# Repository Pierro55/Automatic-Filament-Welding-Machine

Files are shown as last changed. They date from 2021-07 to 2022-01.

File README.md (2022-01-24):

# REuse: Automatic Filament Welding Machine

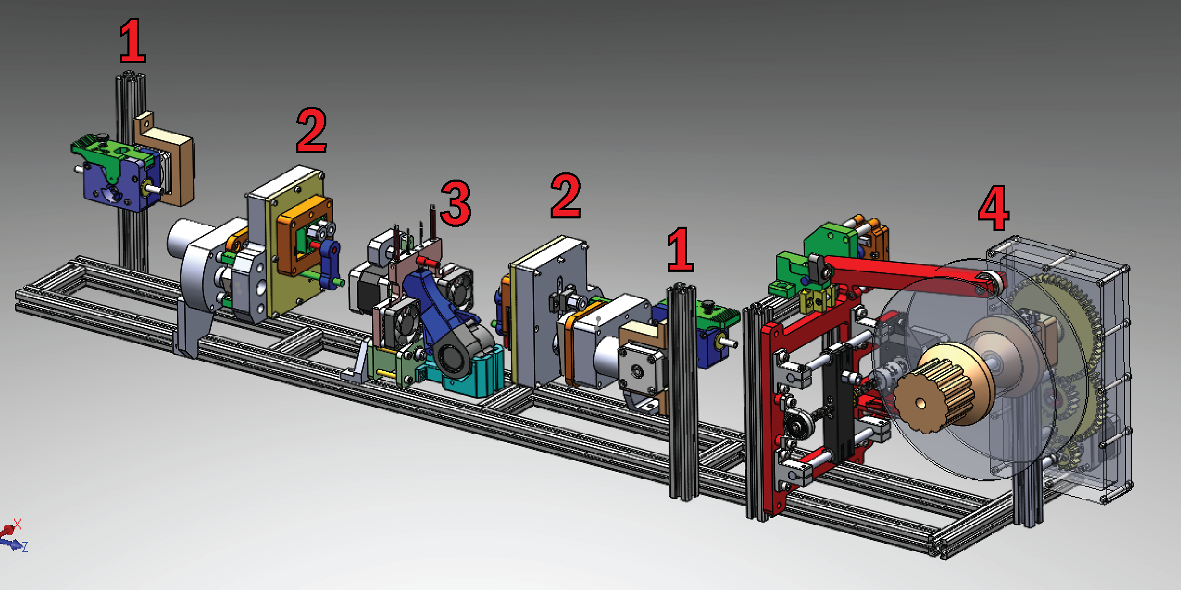
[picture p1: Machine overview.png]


## What is this?
This is an automatic filament welding machine made for 3mm (or 2.85mm) filament. Its purpose is to weld left over filament and wind it on a spool afterwards. The system can be adapted for 1.75mm if needed. 

## General information
I've designed and build this machine as part of my mechanical engineering bachelor thesis. Unfortunately, I didn't had enough time to program and test it thoroughly but tested every single subsystem of the machine itself. The welding part itself works really well. 
All parts are modular and interchangeable. I’ve attached my thesis report which goes into every little detail of the design and building process. It is written in Dutch but translating it should be doable. Maybe I will add an English version in the near future if I get enough requests (or maybe somebody else is so kind to translate it). If you can understand Dutch, please read it with a grain of salt as Dutch isn’t my first language. I will roughly describe every process in English in each folder.
I don't have the machine on hand because I have built it for a company so I cannot make it fully working unfortunately as I don’t have the financial medium to build one myself. Nevertheless, I wanted to make this open source as I have learned a lot through the open source movement about 3D printing and I wanted to give something back to the community. 

If you have any question please do not hesitate to send me a DM on Discord: Pierro55#4076

## Disclaimer
If you try to replicate this machine with the provided data, make sure you work safe. This information is provided for free under the terms of the GPL-2.0 License. Everything is provided without any warranty of any kind. Use the provided information at your own risk, any damage to a machine, device, yourself or similar is solely your own responsibility.

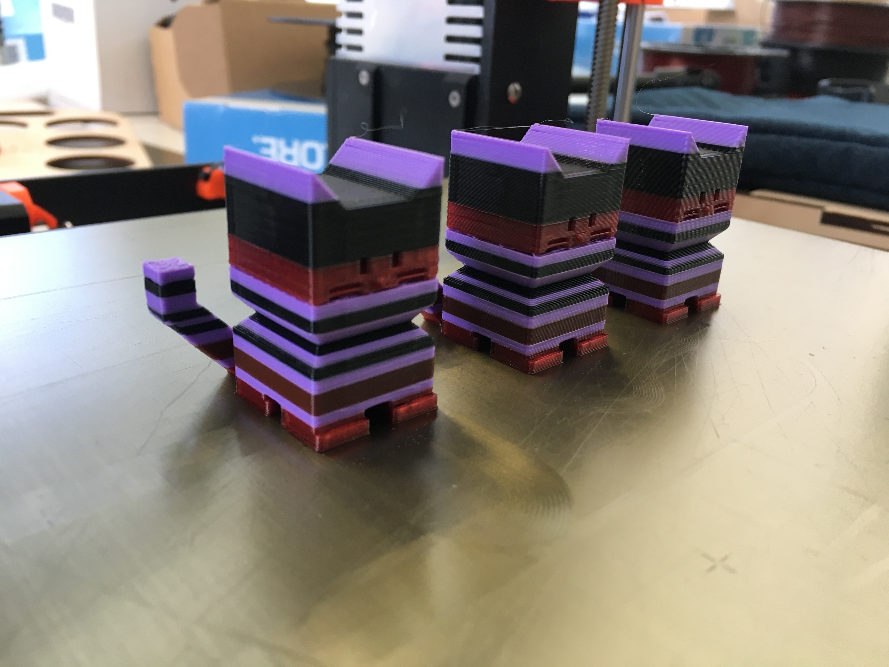
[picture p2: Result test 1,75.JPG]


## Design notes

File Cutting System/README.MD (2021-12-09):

# Cutting system

The cutting system is designed to cut off the filament ends before welding them together and automatically eject the cutoff. The idea behind this system is to make the machine more reliable by controlling the shape of the filament ends. In my experiments I used a geared DC motor for this, which turned out to be too weak. I therefore had to ditch it for the final machine as there wasn’t enough time left. It can still be added to the machine because of its modularity.

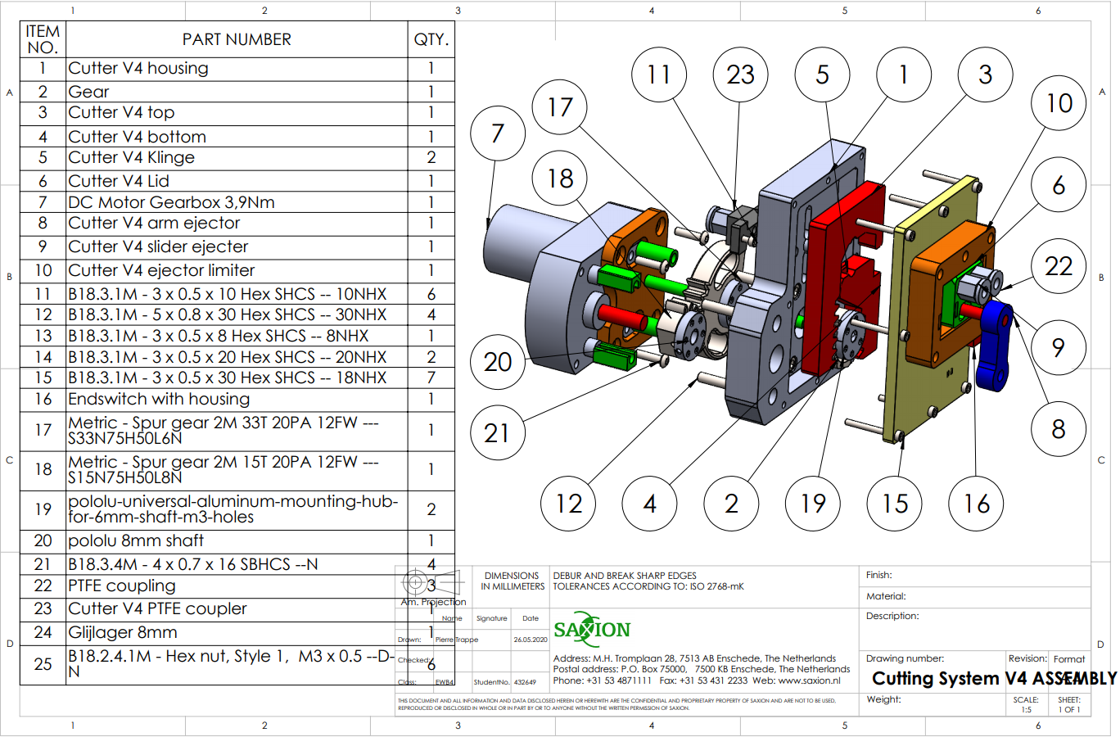
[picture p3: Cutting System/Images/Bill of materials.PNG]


### Basic Principle
The basic principle works as follows:

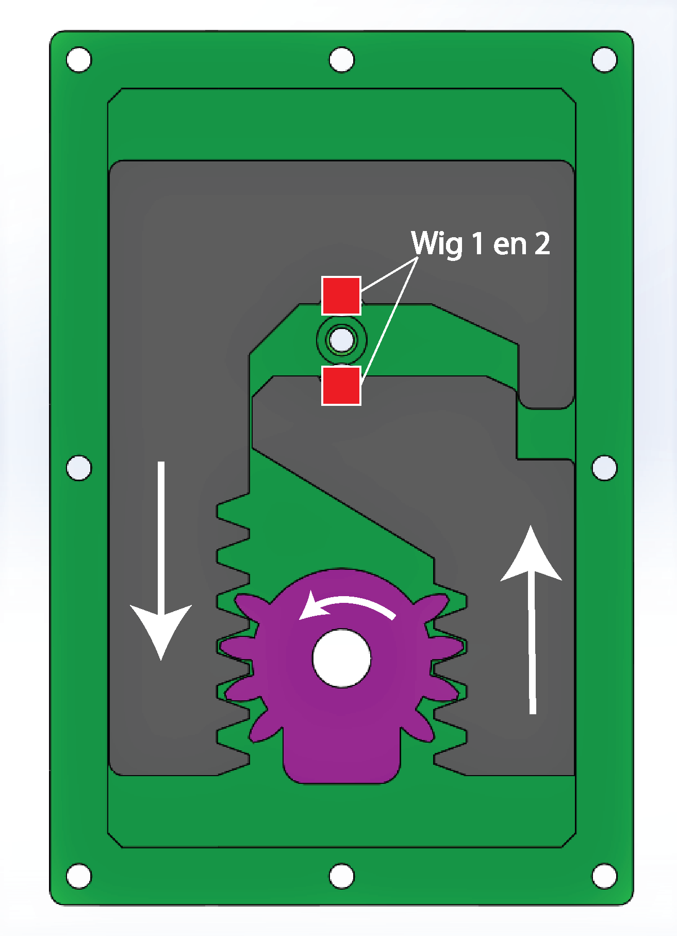
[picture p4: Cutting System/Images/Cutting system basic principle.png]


The purple gear is connected to the motor. This gear moves the left brown arm through a rag pinion mechanism down and the right one up (and vice versa if the motor rotates the other direction). Both arms have a wedge (wig in Dutch) mounted in the middle. As the arms move closer to each other the wedge cuts off filament which sits in the hole between the two arms.
The automatic ejection happens on the outside of the cutting system. As the motor moves the mechanism, a second mechanism, which is directly coupled with the motor shaft, moves two outputs. One is for the cutoff and the second one is for the to be welded filament. 

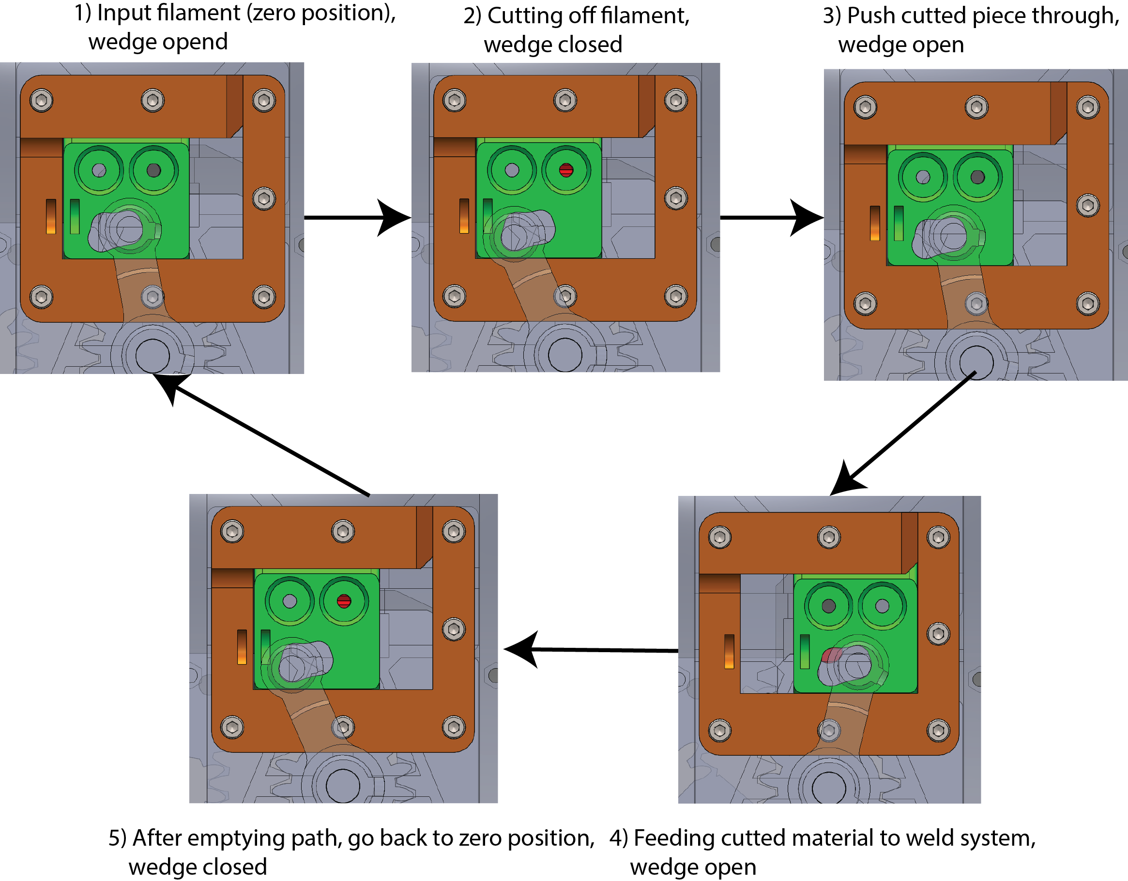
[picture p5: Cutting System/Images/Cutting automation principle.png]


Some rl photos

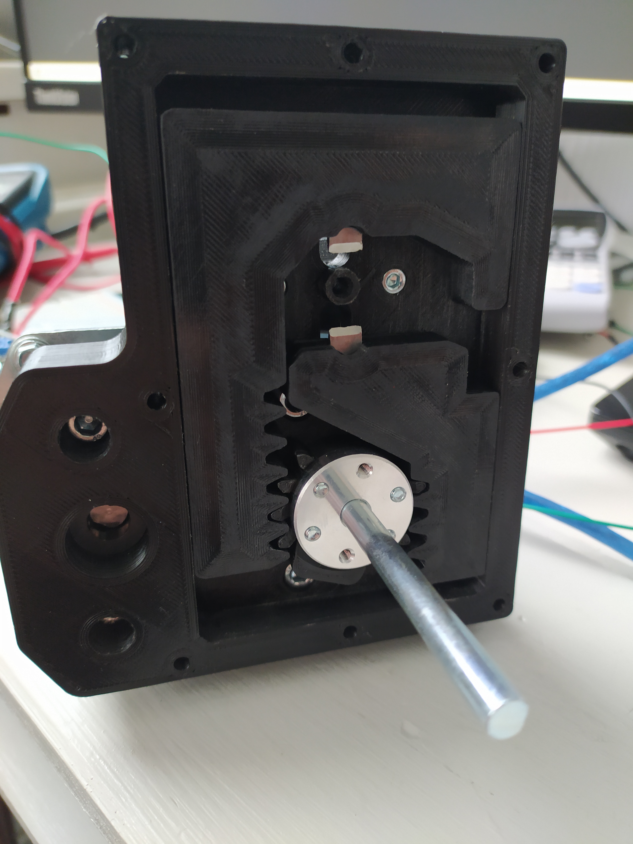
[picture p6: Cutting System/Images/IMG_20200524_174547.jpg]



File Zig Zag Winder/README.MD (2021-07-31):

## Zig Zag Winder

This part of the machine basically takes care of a neat winding of the welded material. It moves the welded material in a zig zag manner when winding it onto a spool.

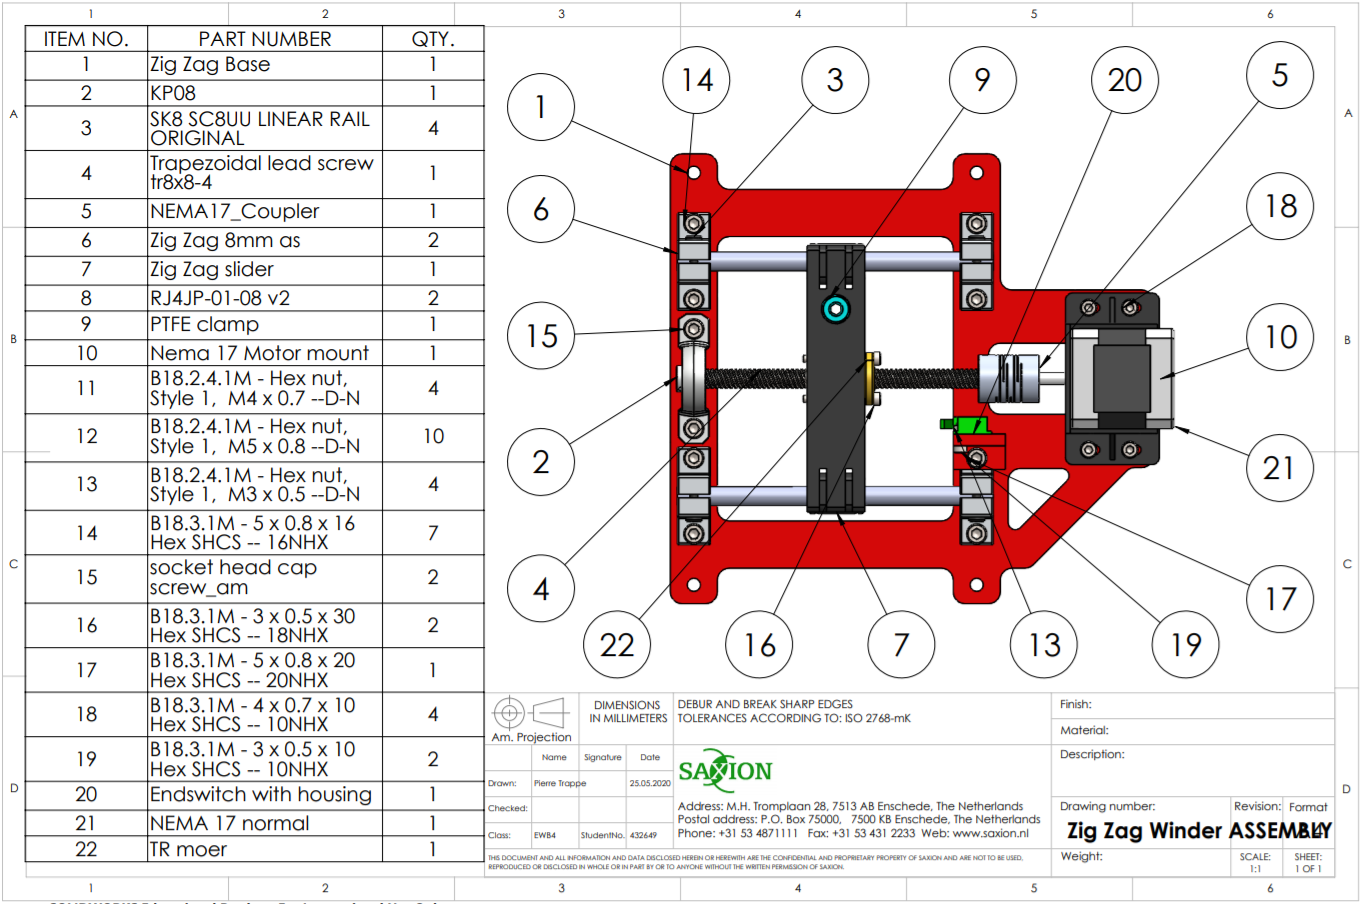
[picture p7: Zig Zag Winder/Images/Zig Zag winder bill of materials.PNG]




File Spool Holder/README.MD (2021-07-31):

# Spool Holder

This part of the machine is designed to drive the winding action and to accept various types of filaments spools. It self-centers the spool when mounting it on the device. It uses a small Nema 17 motor with some gears to beef it up as no fast speeds are needed. It can fit bigger spools when using a longer shaft.

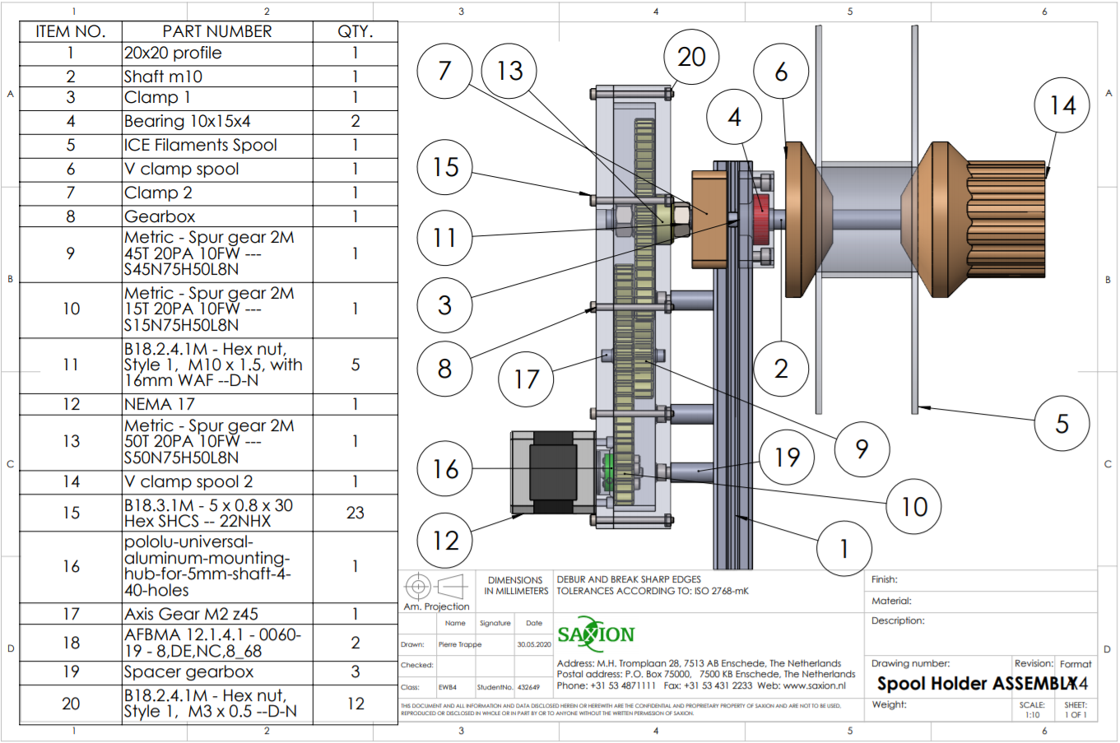
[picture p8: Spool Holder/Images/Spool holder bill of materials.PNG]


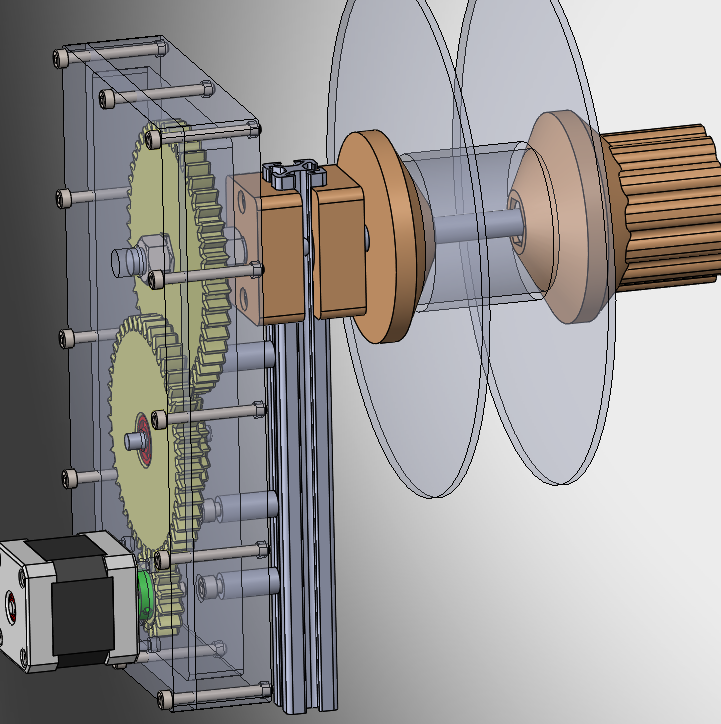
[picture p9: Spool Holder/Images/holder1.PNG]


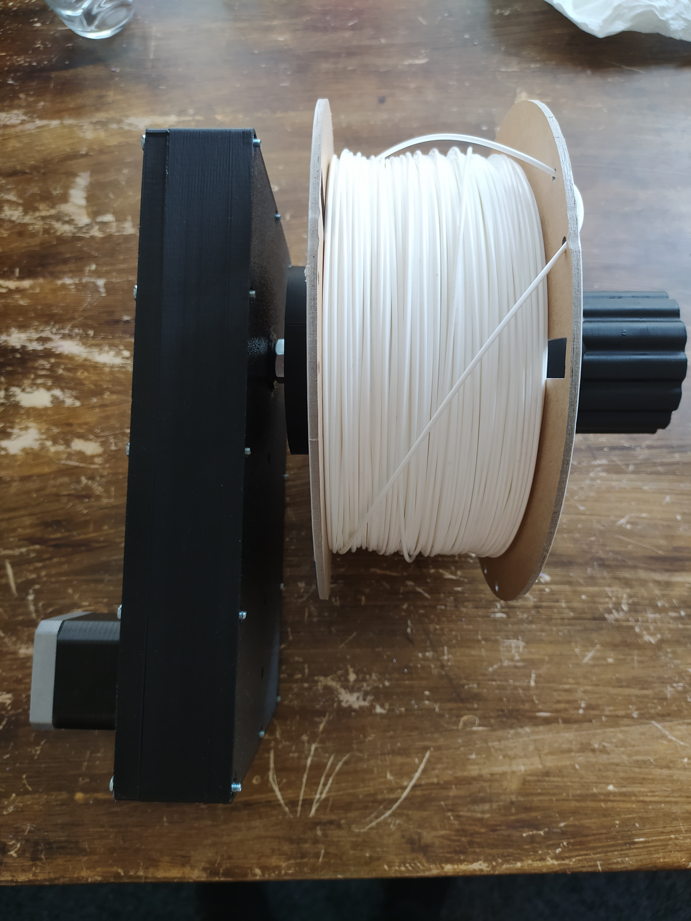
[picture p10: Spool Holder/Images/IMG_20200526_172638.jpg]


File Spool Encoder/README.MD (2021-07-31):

# Spool encoder
This part of the machine keeps track of the material on the spool. This is needed to get information on when the spool is full and also for setting the right winding speed. 

It is basically an arm which sits directly on the spool. The axis of this arm is connected to a potentiometer. As material builds up, the arm goes up and therefore the value of the potentiometer changes. This value gets converted in the software and can be used for said purposes. 

It can be mounted to a 20x20 aluminum extrusion profile.
For ease of use when unmounting a spool, a latch is included in the design to hold the arm up while changing spools.

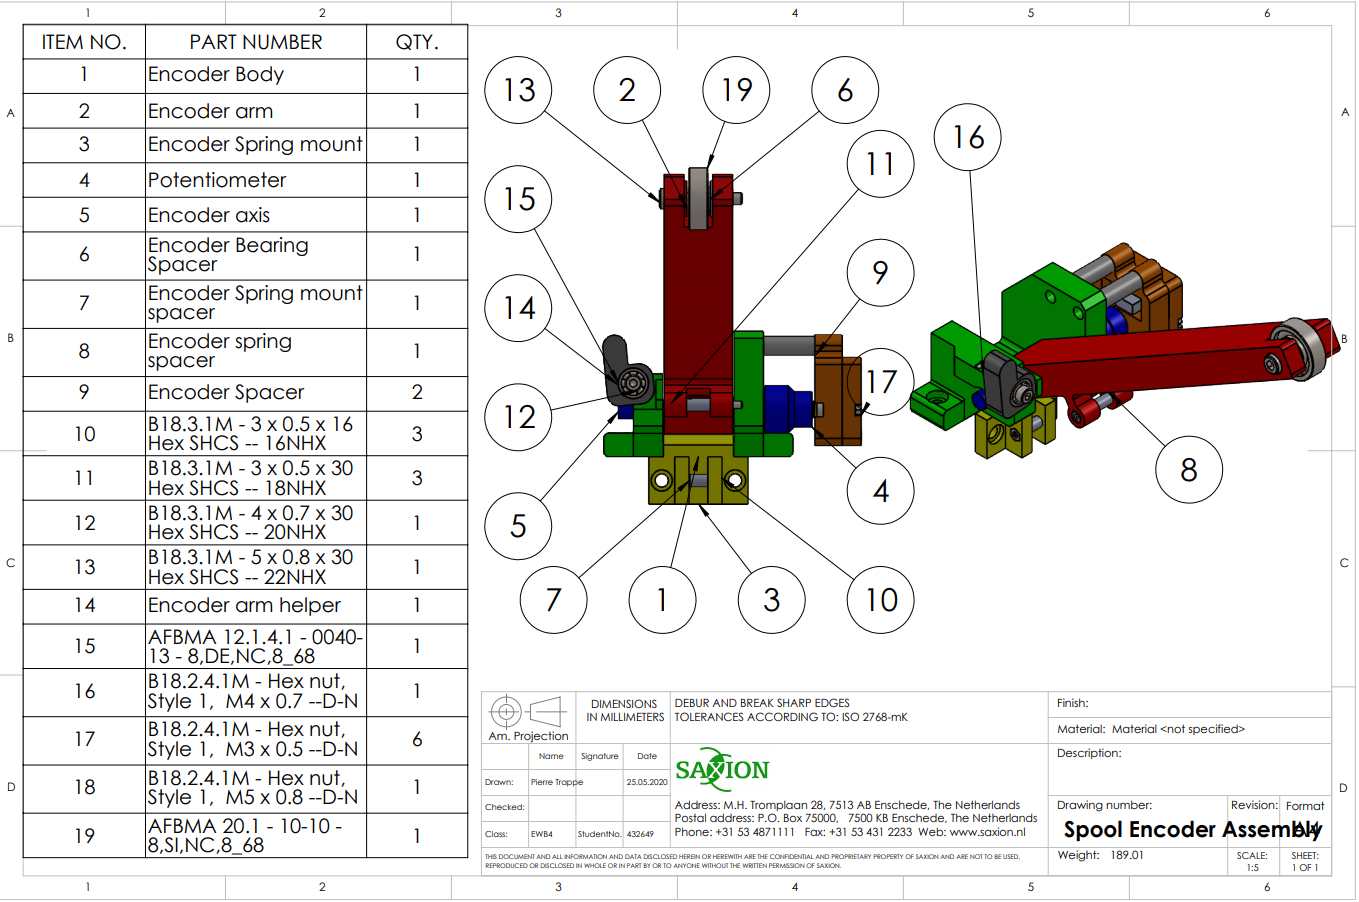
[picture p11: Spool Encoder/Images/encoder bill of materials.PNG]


,

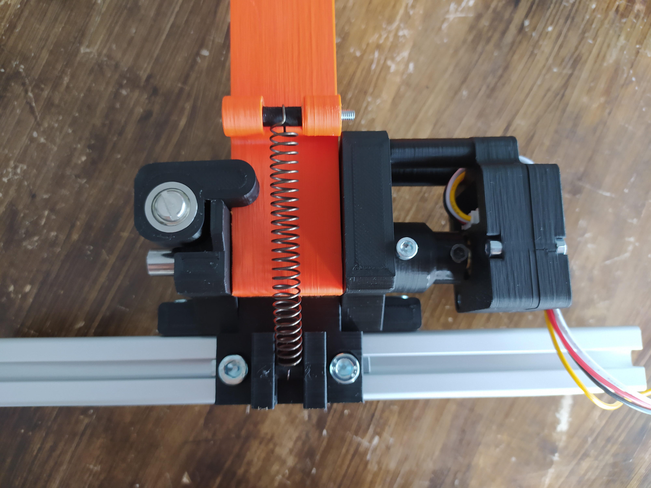
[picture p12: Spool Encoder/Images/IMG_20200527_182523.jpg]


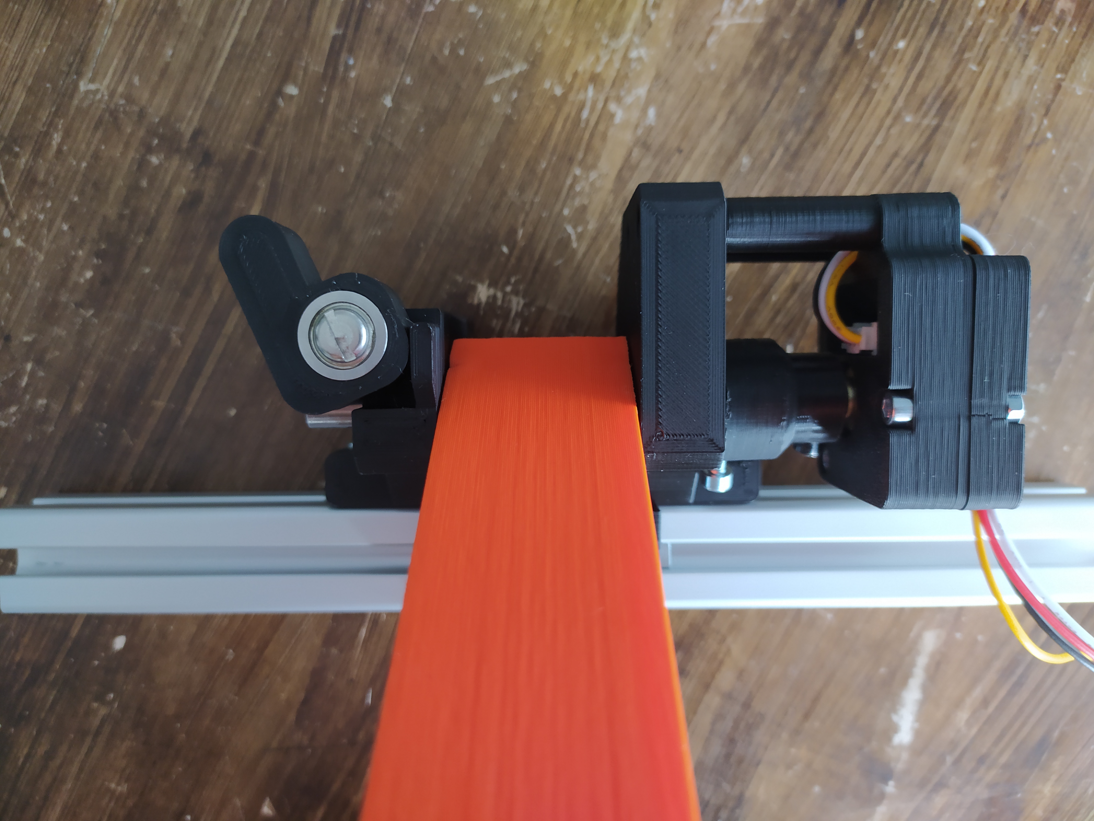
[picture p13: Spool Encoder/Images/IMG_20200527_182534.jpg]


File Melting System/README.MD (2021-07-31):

# Melting System

The melting system can weld two pieces of filament together and also cool the weld afterwards. A first movement test can be seen in the following video:

https://user-images.githubusercontent.com/57869093/126063074-c9a9bbb9-c436-44e4-bffa-66c6a044f957.mp4

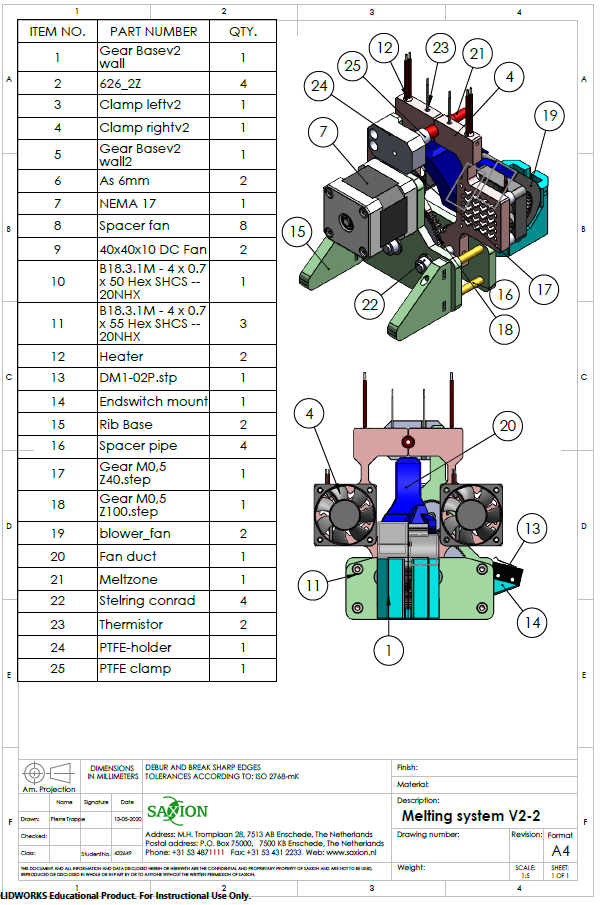
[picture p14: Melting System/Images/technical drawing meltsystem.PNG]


The melt zone itself is made out of PTFE with a honed inner surface of 2.9mm in diameter. The system functions basically as a hotend seen on FDM 3D printers. It has a hot zone and an active cooled cold zone. Two clamps are moved simultaneously to either enabling welding or cooling. 
A result of the welding process can be seen in the following picture:

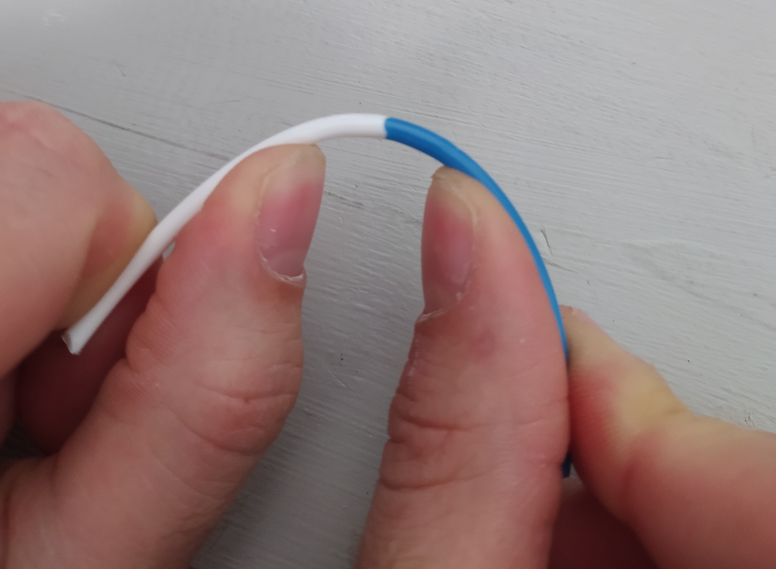
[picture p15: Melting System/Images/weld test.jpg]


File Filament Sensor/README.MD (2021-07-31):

# Filament Sensor

The filament sensor has the purposes to locate the filament position on various locations in the machine. 

The sensor housing uses a compliant mechanism to trigger the mechanical endstop when filament is detected. 

A grooved bearing makes the system bidirectional to ensure that filament can travel back and forth without getting pinched resulting in a jam.

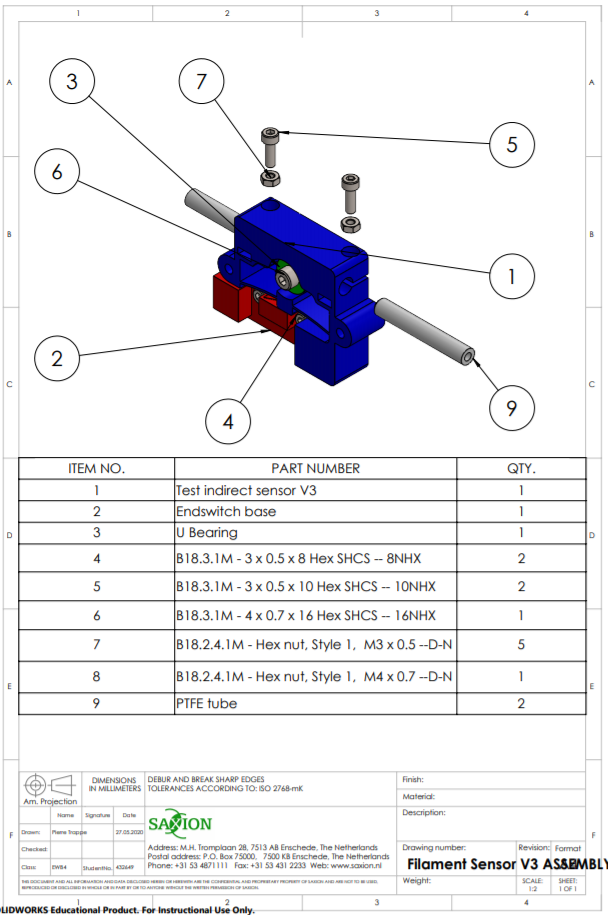
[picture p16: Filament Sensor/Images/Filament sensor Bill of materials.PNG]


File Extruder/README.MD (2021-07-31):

## Extruder

The extruder has the purpose of moving filament through the system. In the final machine, two extruders are used as both ends of filaments needs to be moved individually.

This extruder design uses original Bondtech hardware (hobbed gears, shafts, bearings, 5:1 geared motor...). The housing is 3D printed. 
This design uses 3mm filament. 

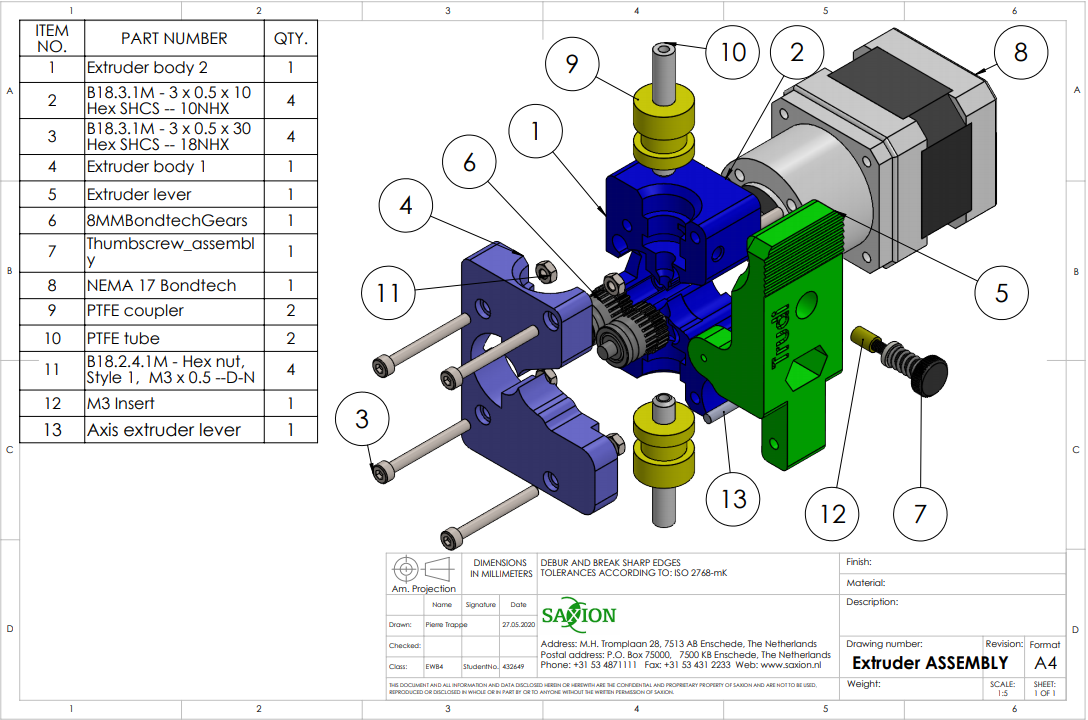
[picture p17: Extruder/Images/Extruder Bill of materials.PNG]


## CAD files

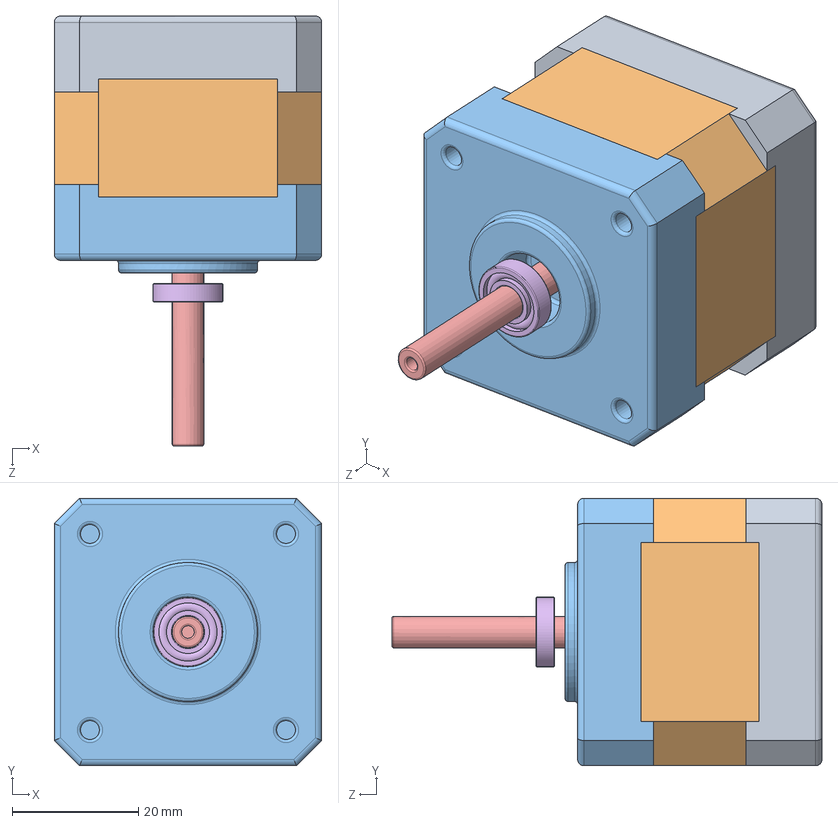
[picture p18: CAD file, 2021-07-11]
Extruder/CAD/NEMA 17.SLDASM
42.3 x 42.3 x 68.0 mm
Base
Cuerpo
Tapa
pan cross head_am x 4
Eje
instrument ball bearing_68_am x 2

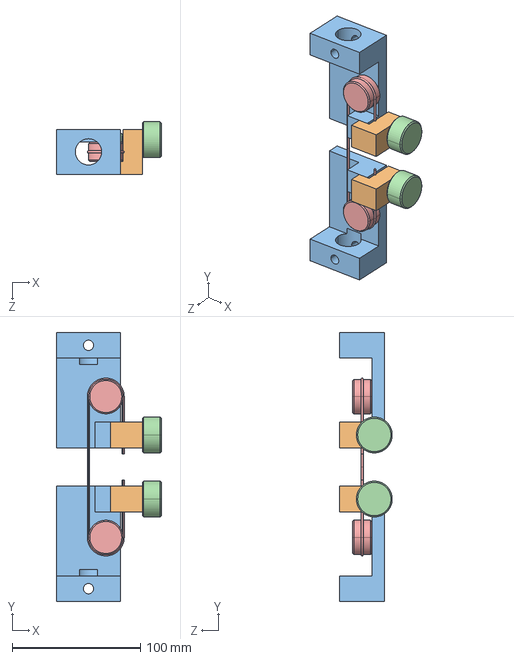
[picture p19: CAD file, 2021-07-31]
Tensile Strength Tester/CAD/Filamenttester ASSEMBLY.STEP
82.0 x 210.0 x 41.0 mm
Filament tester
Filament tester mirrored

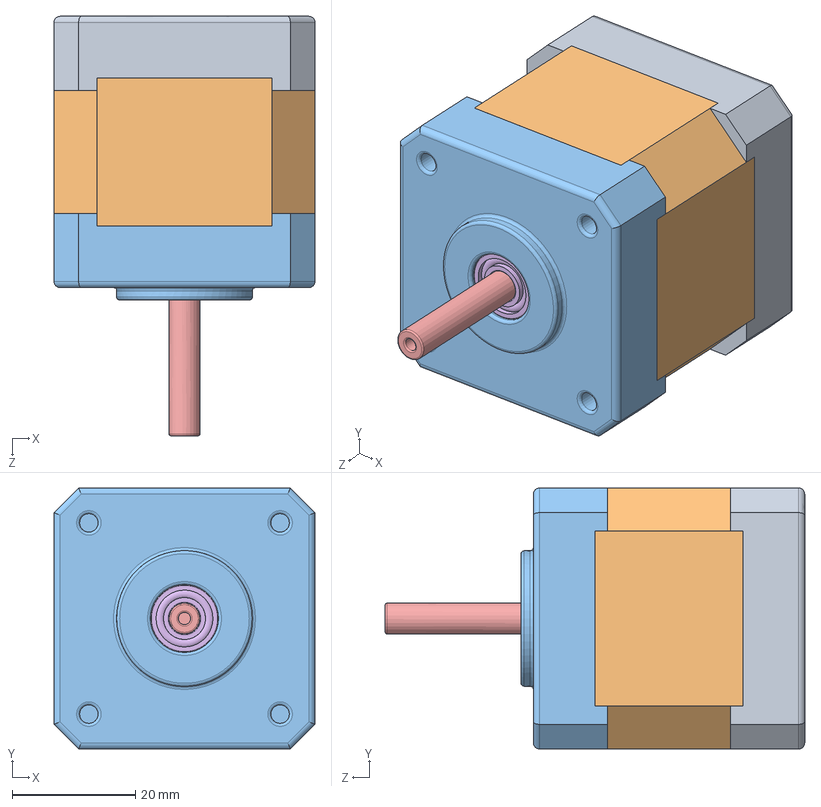
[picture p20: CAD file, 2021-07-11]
Cutting System/CAD/NEMA 17.SLDASM
42.3 x 42.3 x 68.0 mm
Base
Cuerpo
Tapa
pan cross head_am x 4
Eje
instrument ball bearing_68_am x 2

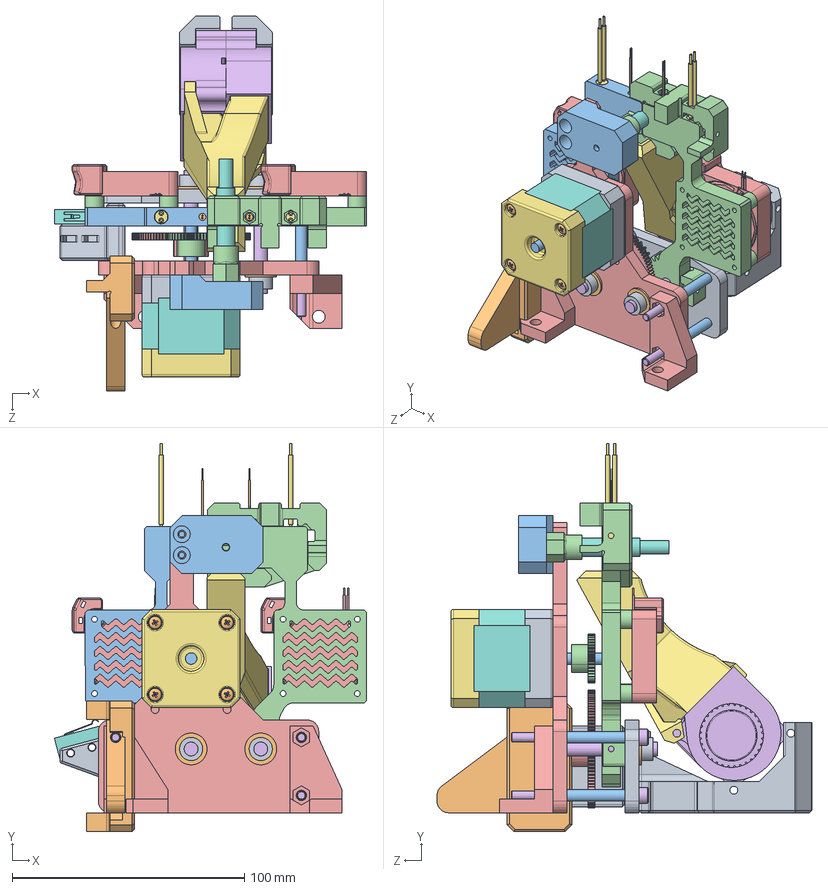
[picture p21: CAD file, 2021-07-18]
Melting System/CAD/Melting system V2-2.SLDASM
134.5 x 167.3 x 161.5 mm
Gear Basev2 wall
626_2Z x 4
Clamp leftv2
Clamp rightv2
Gear Basev2 wall2
As 6mm x 2
Base
Cuerpo
Tapa
pan cross head_am x 4
Eje
Spacer fan x 8
40x40x10 DC Fan x 2
socket head cap screw_am x 4
Heater x 2
DM1-02P.stp
Endswitch mount
Spacer pipe x 4
Gear M0,5 Z40.step
Gear M0,5 Z100.step
blower_fan x 2
Fan duct
Meltzone
Stelring conrad x 4
Thermistor x 2
PTFE-holder
PTFE clamp

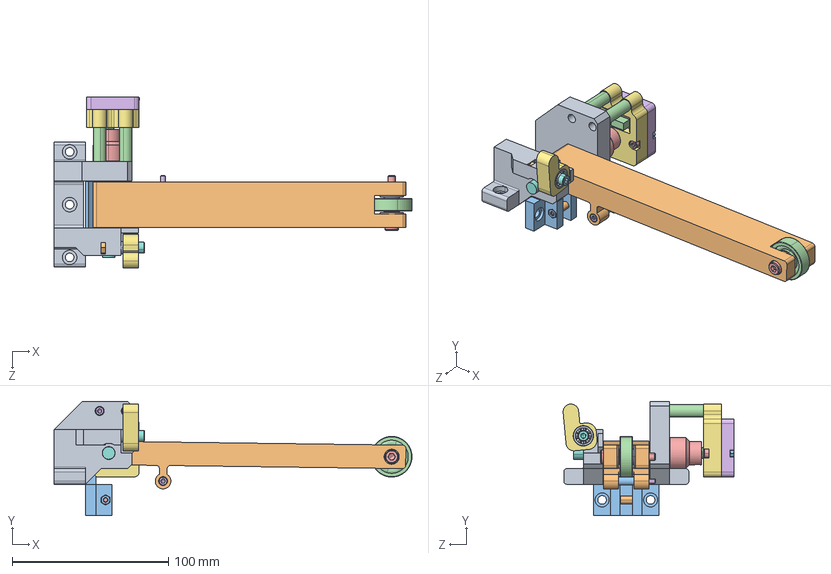
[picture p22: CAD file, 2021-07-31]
Spool Encoder/CAD/Spool Encoder ASSEMBLY.STEP
229.0 x 73.0 x 109.3 mm
Encoder Body
Encoder arm
Encoder Spring mount
Potentiometer
Encoder axis
Encoder Bearing Spacer
Encoder Spring mount spacer
Encoder spring spacer
Encoder Spacer x 2
socket head cap screw_am_B18.3.1M - 3 x 0.5 x 16 Hex SHCS -- 16NHX x 3
socket head cap screw_am_B18.3.1M - 3 x 0.5 x 30 Hex SHCS -- 18NHX x 3
Encoder arm helper
socket head cap screw_am_B18.3.1M - 4 x 0.7 x 30 Hex SHCS -- 20NHX
instrument ball bearing_68_am_AFBMA 12.1.4.1 - 0040-13 - 8,DE,NC,8_68
hex nut style 1_am_B18.2.4.1M - Hex nut, Style 1, M4 x 0.7 --D-N
hex nut style 1_am_B18.2.4.1M - Hex nut, Style 1, M3 x 0.5 --D-N x 6
radial ball bearing_68_am_AFBMA 20.1 - 10-10 - 8,SI,NC,8_68
socket head cap screw_am_B18.3.1M - 5 x 0.8 x 30 Hex SHCS -- 22NHX
hex nut style 1_am_B18.2.4.1M - Hex nut, Style 1, M5 x 0.8 --D-N

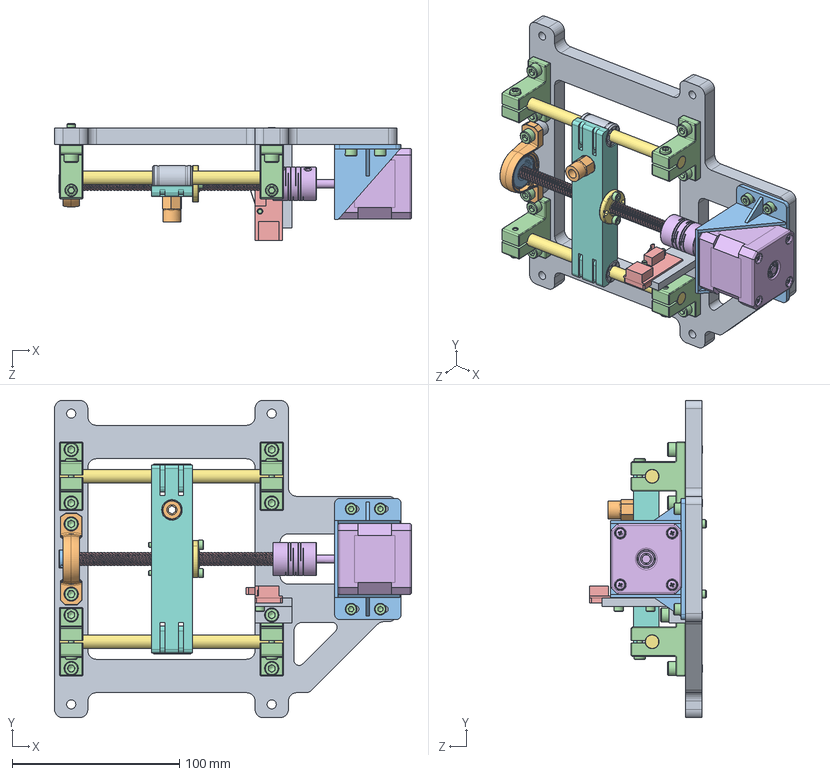
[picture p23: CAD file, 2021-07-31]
Zig Zag Winder/CAD/Zig Zag Winder ASSEMBLY.SLDASM
213.6 x 190.0 x 69.9 mm
Zig Zag Base
KP08
608RS
SK8 SC8UU LINEAR RAIL ORIGINAL x 4
Trapezoidal lead screw tr8x8-4
NEMA17_Coupler
Zig Zag 8mm as x 2
Zig Zag slider
RJ4JP-01-08 v2 x 2
PTFE clamp
Nema 17 Motor mount
socket head cap screw_am x 18
Endswitch with housing
NEMA 17 normal
TR moer

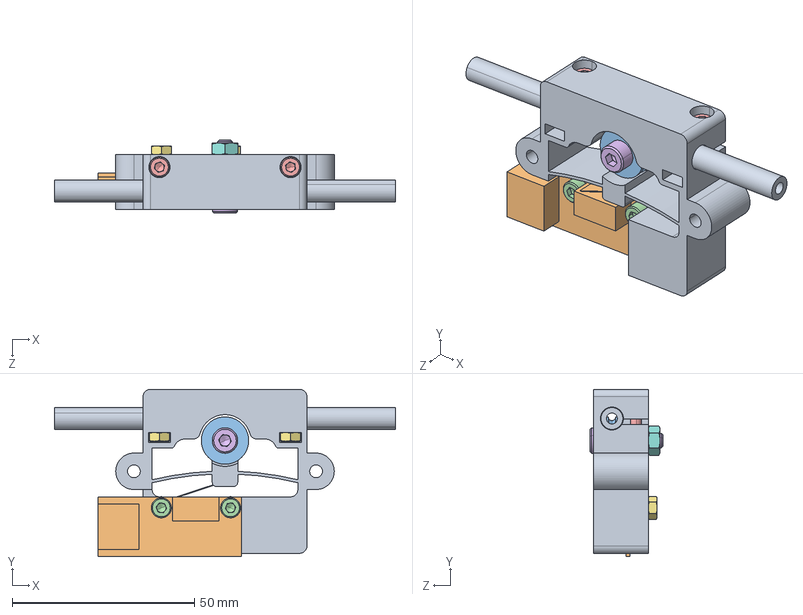
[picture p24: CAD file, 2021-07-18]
Filament Sensor/CAD/Filament Sensor V3 ASSEMBLY.STEP
93.6 x 45.9 x 20.0 mm
Test indirect sensor V3
Endswitch base
U Bearing
socket head cap screw_am_B18.3.1M - 3 x 0.5 x 8 Hex SHCS -- 8NHX x 2
socket head cap screw_am_B18.3.1M - 3 x 0.5 x 10 Hex SHCS -- 10NHX x 2
socket head cap screw_am_B18.3.1M - 4 x 0.7 x 16 Hex SHCS -- 16NHX
hex nut style 1_am_B18.2.4.1M - Hex nut, Style 1, M3 x 0.5 --D-N x 5
hex nut style 1_am_B18.2.4.1M - Hex nut, Style 1, M4 x 0.7 --D-N
PTFE tube x 2

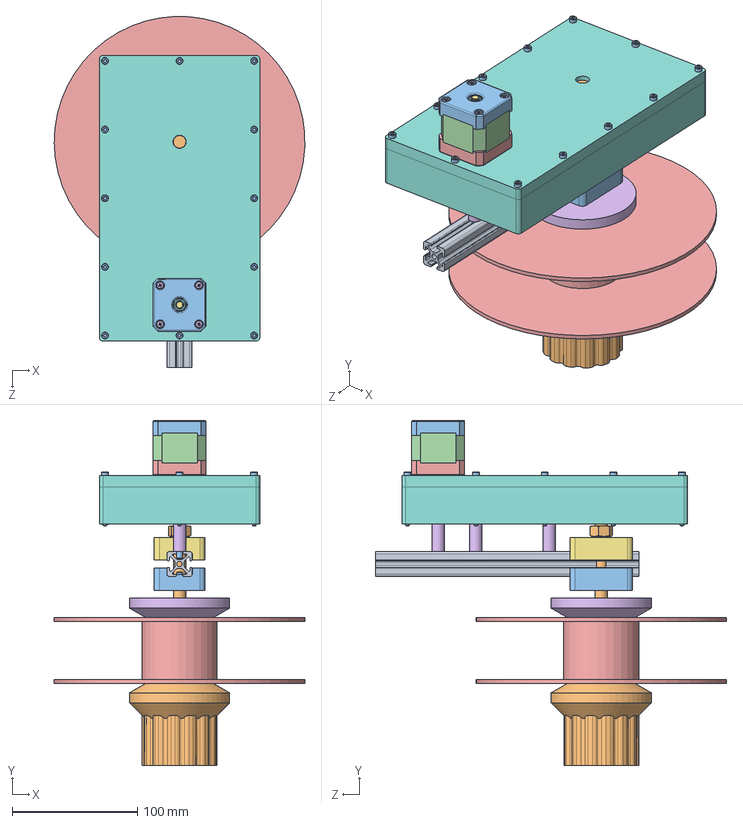
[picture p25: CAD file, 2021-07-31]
Spool Holder/CAD/Spool Holder ASSEMBLY.SLDASM
199.9 x 275.2 x 279.9 mm
20x20 profile
Shaft m10
Clamp 1
Bearing 10x15x4 x 2
ICE Filaments Spool
V clamp spool
Clamp 2
Gearbox
spur gear_am x 3
hex nut style 1_am x 17
Base
Cuerpo
Tapa
pan cross head_am x 4
Eje
instrument ball bearing_68_am x 4
Gear m2 z20
V clamp spool 2
socket head cap screw_am x 23
pololu-universal-aluminum-mounting-hub-for-5mm-shaft-4-40-holes
Axis Gear M2 z45
Spacer gearbox x 3

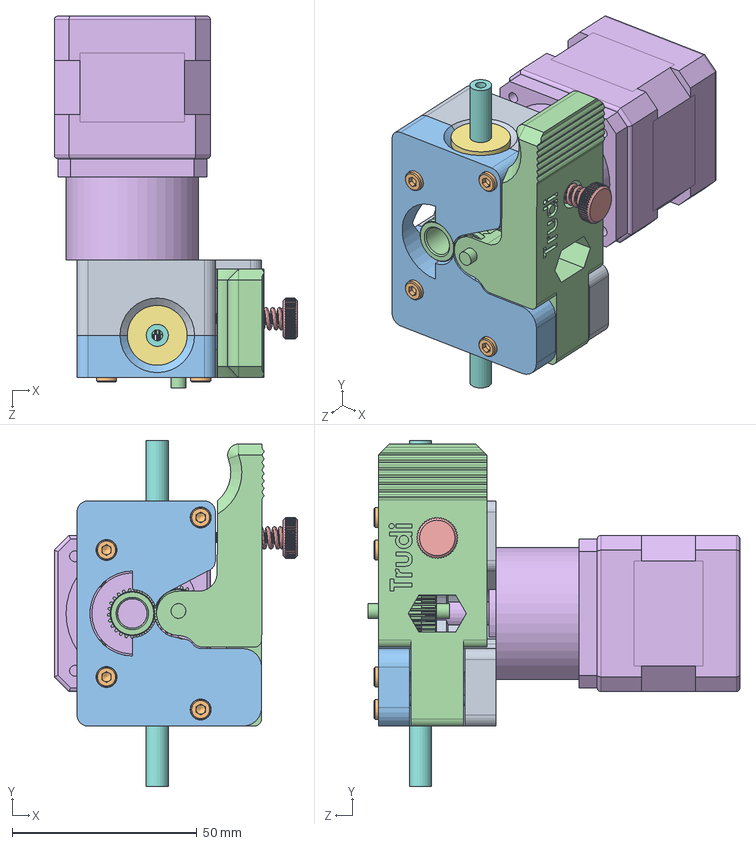
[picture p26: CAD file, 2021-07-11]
Extruder/CAD/Extruder ASSEMBLY.SLDASM
65.9 x 93.7 x 100.7 mm
Extruder body 2
socket head cap screw_am x 8
Extruder body 1
Extruder lever
Thumbscrew_assembly
NEMA 17 Bondtech
PTFE coupler x 2
PTFE tube x 2
hex nut style 1_am x 4
M3 Insert
Axis extruder lever
8MMBondtechGears

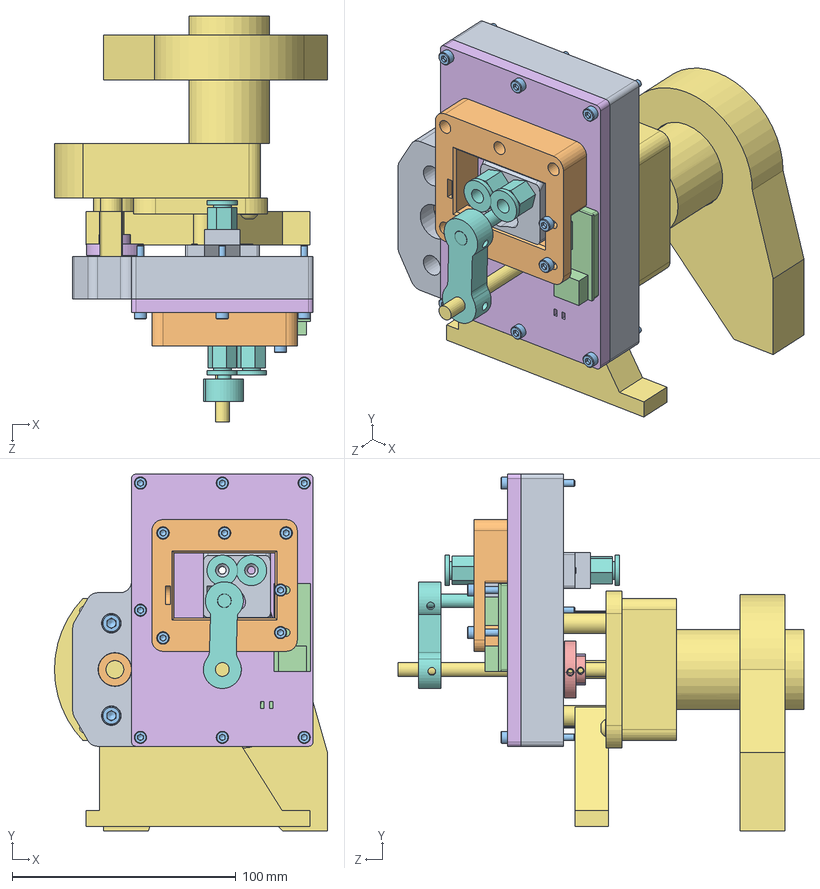
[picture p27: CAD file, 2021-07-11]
Cutting System/CAD/Cutting System V4 ASSEMBLY.SLDASM
122.0 x 159.4 x 181.4 mm
Cutter V4 housing
Gear
Cutter V4 top
Cutter V4 bottom
Cutter V4 Klinge x 2
Cutter V4 Lid
DC Motor Gearbox 3,9Nm
Cutter V4 arm ejector
Cutter V4 slider ejecter
Cutter V4 ejector limiter
socket head cap screw_am x 20
Endswitch with housing
pololu-universal-aluminum-mounting-hub-for-6mm-shaft-m3-holes x 2
pololu 8mm shaft
socket button head cap screw_am x 4
PTFE coupling x 3
Cutter V4 PTFE coupler
Glijlager 8mm
hex nut style 1_am x 6

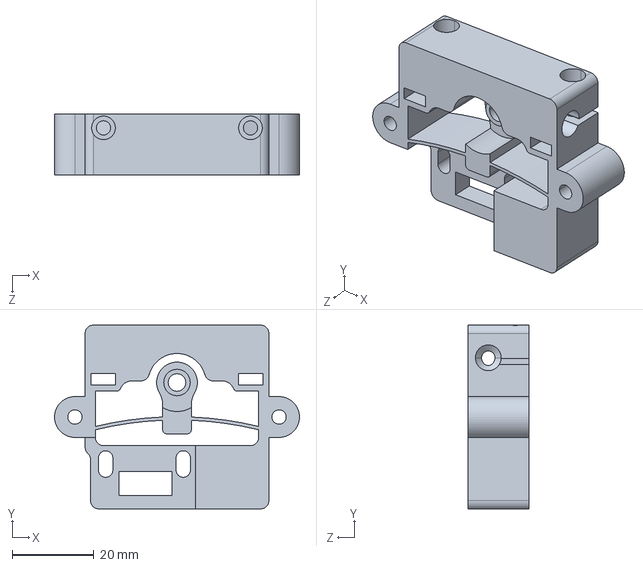
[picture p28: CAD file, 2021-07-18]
Filament Sensor/CAD/Test indirect sensor V3.STEP
60.0 x 45.0 x 15.0 mm

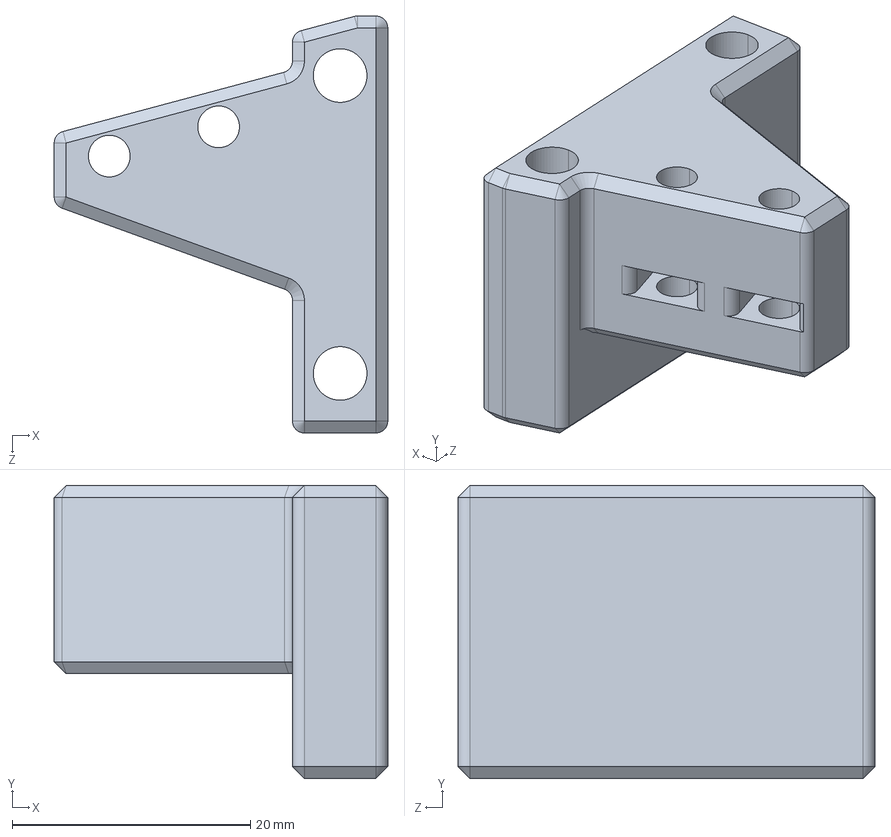
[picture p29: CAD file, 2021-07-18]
Melting System/CAD/Endswitch mount.STEP
28.0 x 24.6 x 35.0 mm

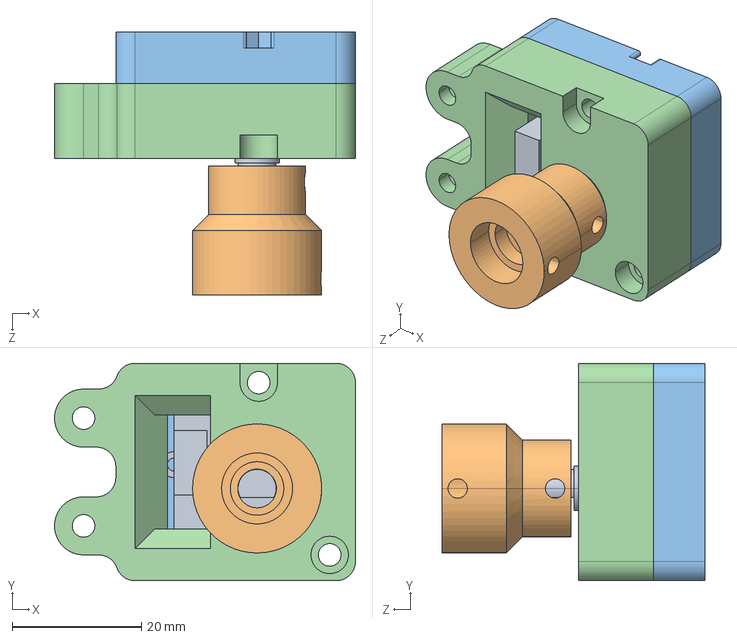
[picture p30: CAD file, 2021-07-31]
Spool Encoder/CAD/Potentiometer.STEP
46.6 x 33.7 x 40.8 mm

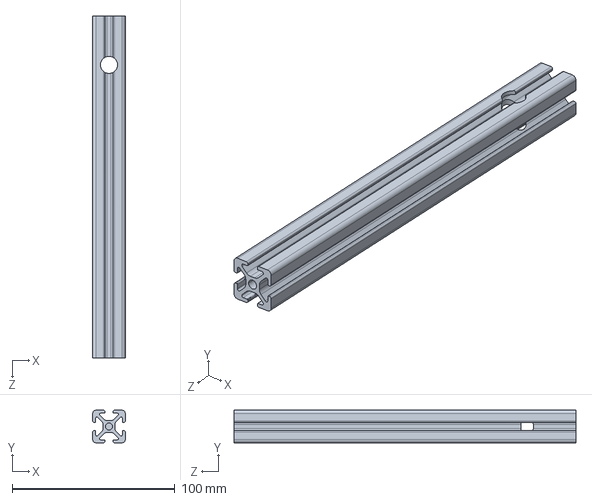
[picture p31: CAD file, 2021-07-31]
Spool Holder/CAD/20x20 profile.STEP
20.0 x 20.0 x 210.0 mm

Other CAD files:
Cutting System/CAD/626_Z.sldasm
Zig Zag Winder/CAD/PTFE clamp.STEP
Extruder/CAD/Extruder body 2.STEP
Filament Sensor/CAD/PTFE tube.STEP
Cutting System/CAD/Cutter V4 Klinge.SLDPRT
Cutting System/CAD/Cutter V4 Klinge.STEP
Cutting System/CAD/Cutter V4 Lid.STEP
Cutting System/CAD/Cutter V4 Lid.sldprt
Cutting System/CAD/Cutter V4 PTFE coupler.STEP
Cutting System/CAD/Cutter V4 PTFE coupler.sldprt
Cutting System/CAD/Cutter V4 arm ejector.STEP
Cutting System/CAD/Cutter V4 arm ejector.sldprt
Cutting System/CAD/Cutter V4 bottom.STEP
Cutting System/CAD/Cutter V4 bottom.sldprt
Cutting System/CAD/Cutter V4 ejector limiter.STEP
Cutting System/CAD/Cutter V4 ejector limiter.sldprt
Cutting System/CAD/Cutter V4 housing.STEP
Cutting System/CAD/Cutter V4 housing.sldprt
Cutting System/CAD/Cutter V4 slider ejecter.STEP
Cutting System/CAD/Cutter V4 slider ejecter.sldprt
Cutting System/CAD/Cutter V4 top.STEP
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

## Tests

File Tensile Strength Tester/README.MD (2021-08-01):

## Tensile Tester

This device is just an addon and not needed for the machine. I've built it to be able to measure the tensile strength of normal filament and compare the result with my welded filament to get somewhat scientific data showing the strength of the seam.

I've designed this inspired by other already existing devices. Because I like things organized, I've also created a storage box which is not included in the files (I can upload it if there is any interest in it).

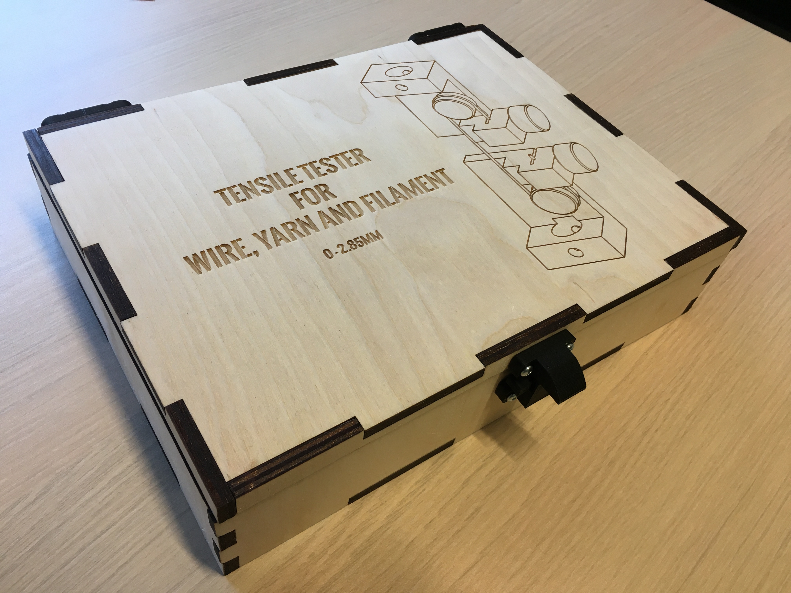
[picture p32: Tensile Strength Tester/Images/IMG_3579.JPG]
   
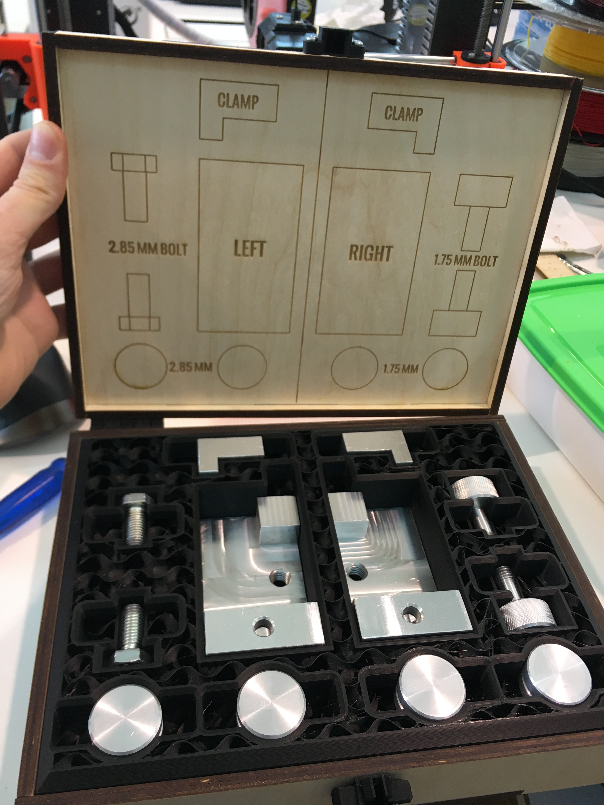
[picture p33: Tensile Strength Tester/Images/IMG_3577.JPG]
 
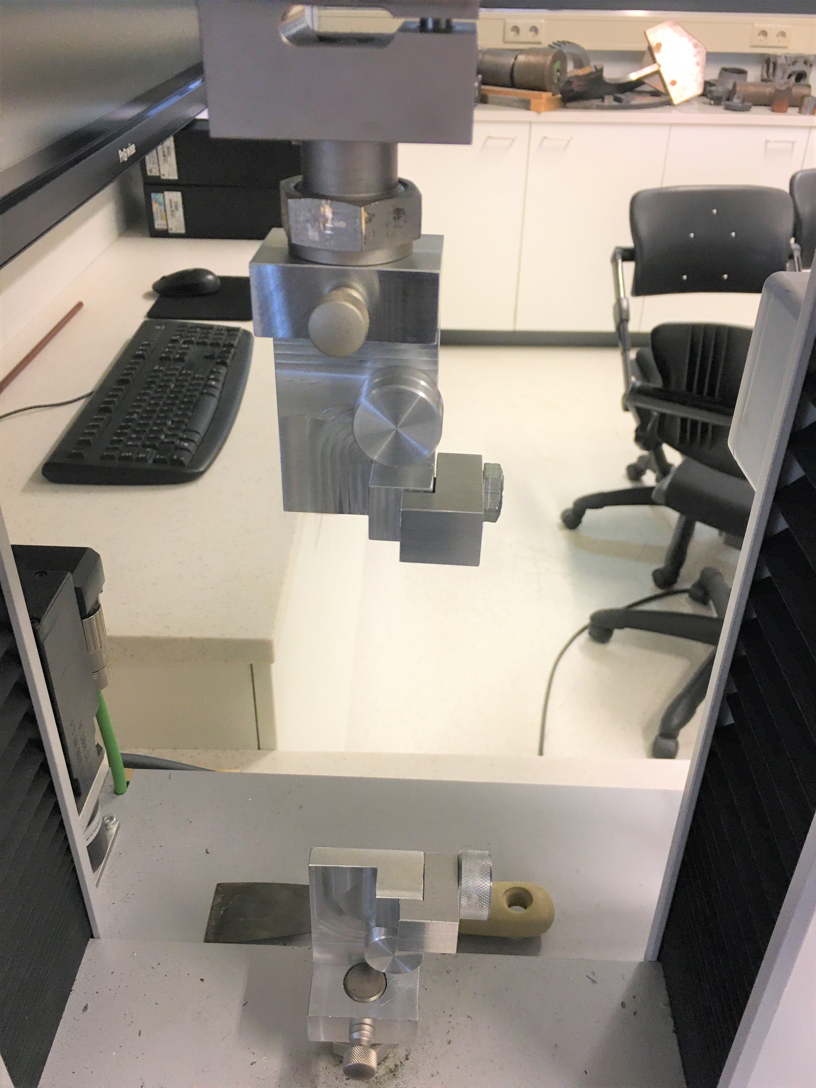
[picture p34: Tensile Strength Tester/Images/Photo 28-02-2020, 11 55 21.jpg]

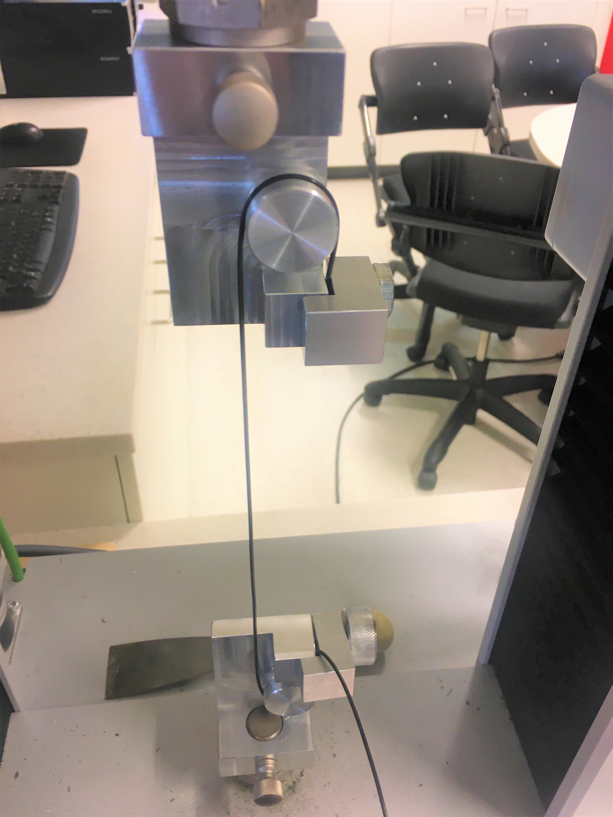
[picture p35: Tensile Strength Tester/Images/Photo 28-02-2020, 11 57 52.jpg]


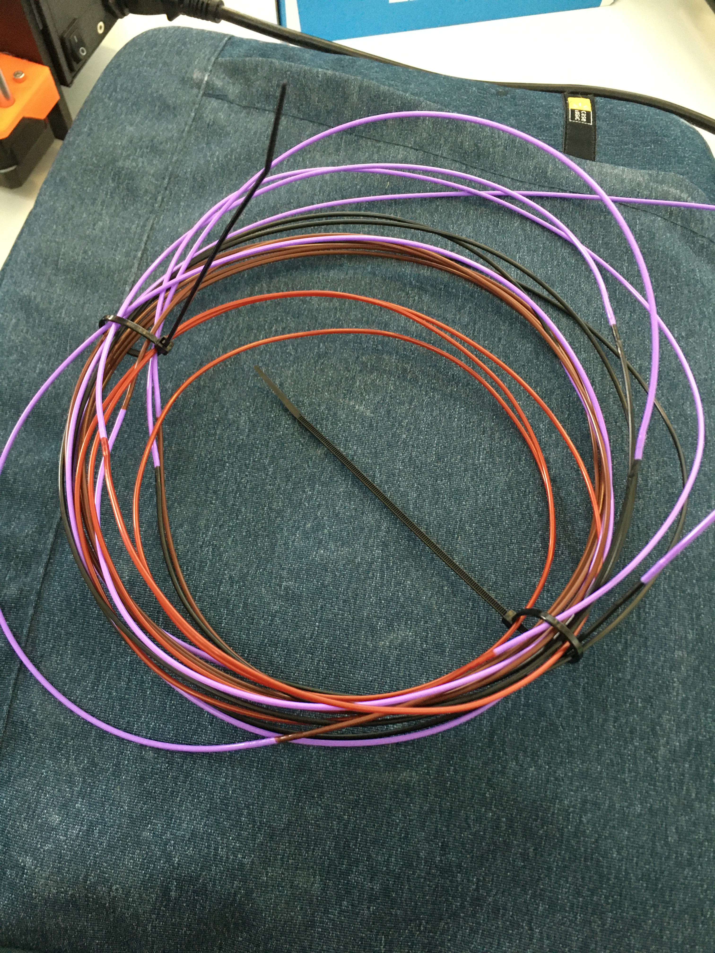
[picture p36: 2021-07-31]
Result 1 test 1,75.JPG

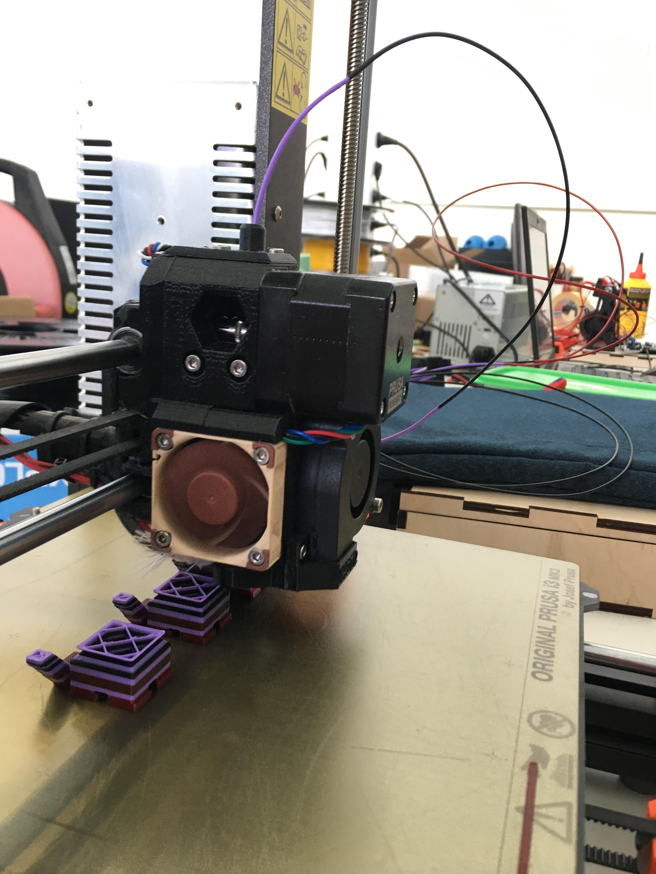
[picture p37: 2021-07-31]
Result 2 test 1,75.JPG

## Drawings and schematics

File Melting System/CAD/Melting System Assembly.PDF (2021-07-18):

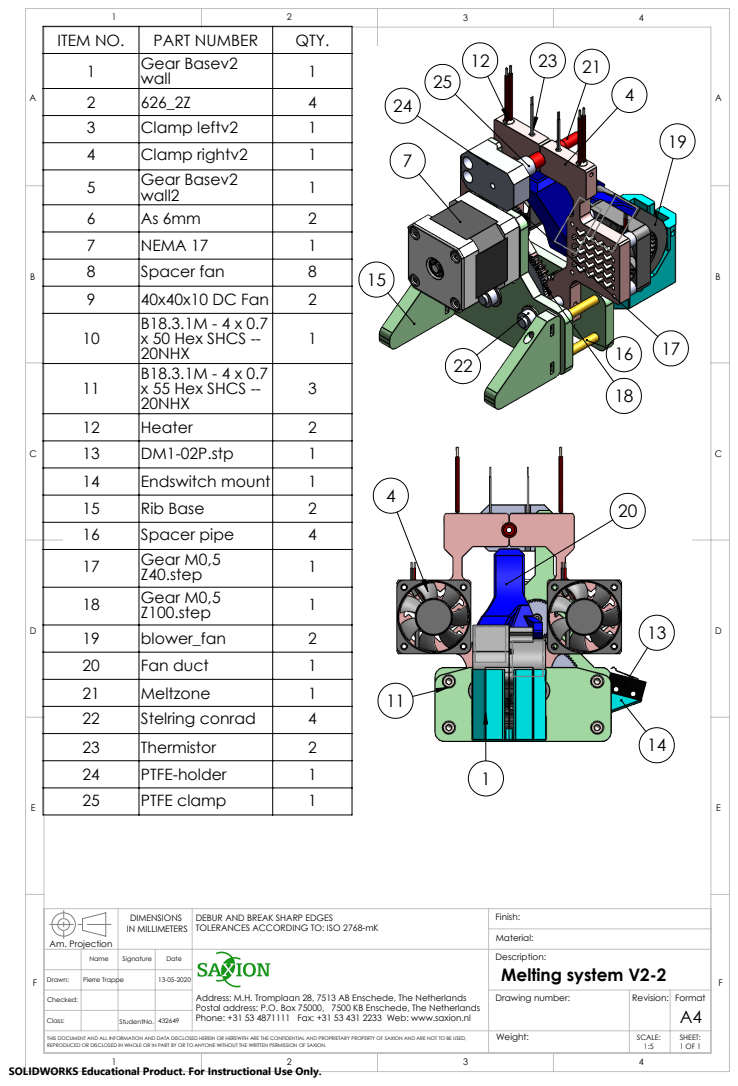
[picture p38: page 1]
IN MILLIMETERS; Am. Projection

ITEM NO. | PART NUMBER | QTY.
1 | Gear Basev2 wall | 1
2 | 626_2Z | 4
3 | Clamp leftv2 | 1
4 | Clamp rightv2 | 1
5 | Gear Basev2 wall2 | 1
6 | As 6mm | 2
7 | NEMA 17 | 1
8 | Spacer fan | 8
9 | 40x40x10 DC Fan | 2
10 | B18.3.1M - 4 x 0.7 x 50 Hex SHCS --20NHX | 1

C | 11 | B18.3.1M - 4 x 0.7 x 55 Hex SHCS --20NHX | 3

12 | Heater | 2
13 | DM1-02P.stp | 1
14 | Endswitch mount | 1
15 | Rib Base | 2
16 | Spacer pipe | 4
17 | Gear M0,5 Z40.step | 1
18 | Gear M0,5 Z100.step | 1

19 | blower_fan | 2
20 | Fan duct | 1
21 | Meltzone | 1
22 | Stelring conrad | 4
23 | Thermistor | 2
24 | PTFE-holder | 1
25 | PTFE clamp | 1

DEBUR AND BREAK SHARP EDGES
TOLERANCES ACCORDING TO: ISO 2768-mK

Name | Signature | Date | Address: M.H. Tromplaan 28, 7513 AB Enschede, The Netherlands Postal address: P.O. Box 75000, 7500 KB Enschede, The Netherlands | Description: Melting system V2-2

Drawn: | Pierre Trappe | | 13-05-2020

Checked: | | | | | Drawing number: | Revision: | Format A4 SCALE:

Class: | | | 432649 | Phone: +31 53 4871111 Fax: +31 53 431 2233 Web: www.saxion.nl StudentNo.
THIS DOCUMENT AND ALL INFORMATION AND DATA DISCLOSED HEREIN OR HEREWITH ARE THE CONFIDENTIAL AND PROPRIETARY PROPERTY OF SAXION AND ARE NOT TO BE USED, REPRODUCED OR DISCLOSED IN WHOLE OR IN PART BY OR TO ANYONE WITHOUT THE WRITTEN PERMISSION OF SAXION. | | | | | Weight: | 1:5 | SHEET:

SOLIDWORKS Educational Product. For Instructional Use Only.

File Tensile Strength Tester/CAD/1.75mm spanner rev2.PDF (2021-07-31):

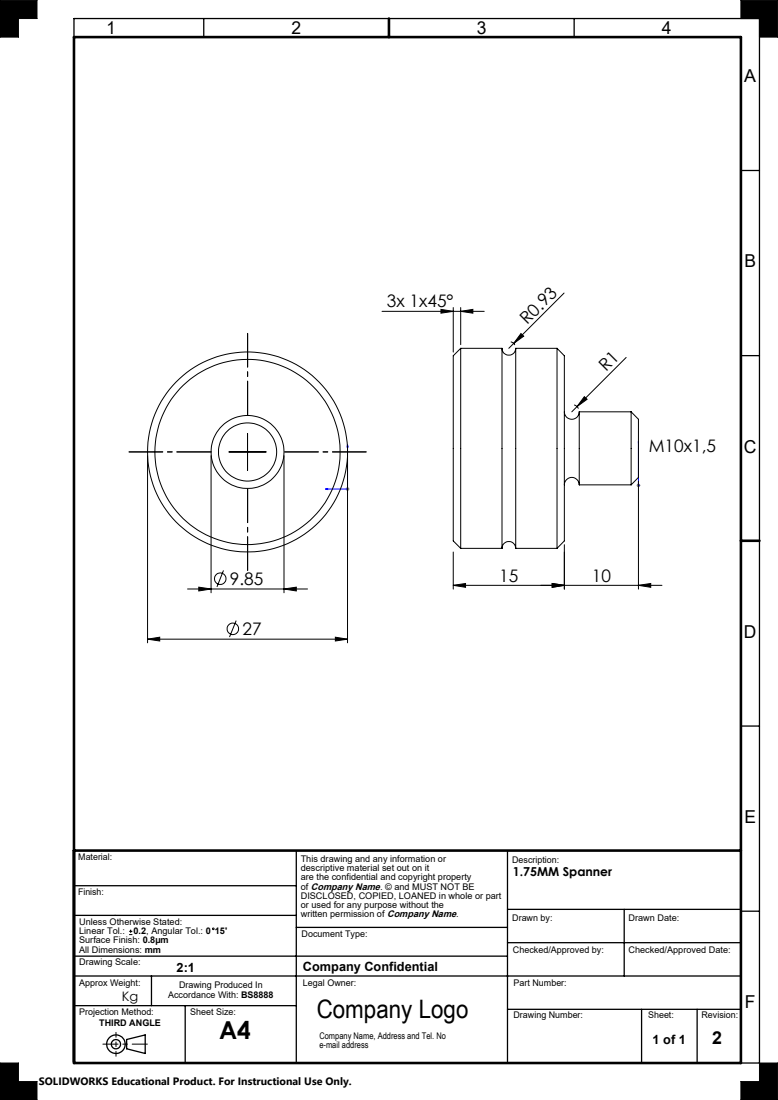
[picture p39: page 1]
Company Logo; Part Number:; Drawing Number:; Sheet:; Revision:; Approx Weight:; Legal Owner:; Projection Method: THIRD ANGLE; Drawn by:; Drawn Date:; Document Type:; 1.75MM Spanner

This drawing and any information or
descriptive material set out on it
are the confidential and copyright property
of Company Name. © and MUST NOT BE
DISCLOSED, COPIED, LOANED in whole or part
or used for any purpose without the

Finish:
written permission of Company Name. Unless Otherwise Stated:
Linear Tol.: 0.2, Angular Tol.: 0 15'
Surface Finish: 0.8µm
All Dimensions: mm
Company Confidential Drawing Scale:

Checked/Approved by:

Checked/Approved Date:

Drawing Produced In
Accordance With: BS8888
Sheet Size:

Company Name, Address and Tel. No
e-mail address

SOLIDWORKS Educational Product. For Instructional Use Only.
